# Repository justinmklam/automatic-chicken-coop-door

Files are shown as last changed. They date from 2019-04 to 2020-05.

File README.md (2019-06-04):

# Automatic Chicken Coop Door

Automatic chicken coop door for my backyard egg layers. Modeled after the commercially available [Chicken Guard](https://www.chickenguard.com/).

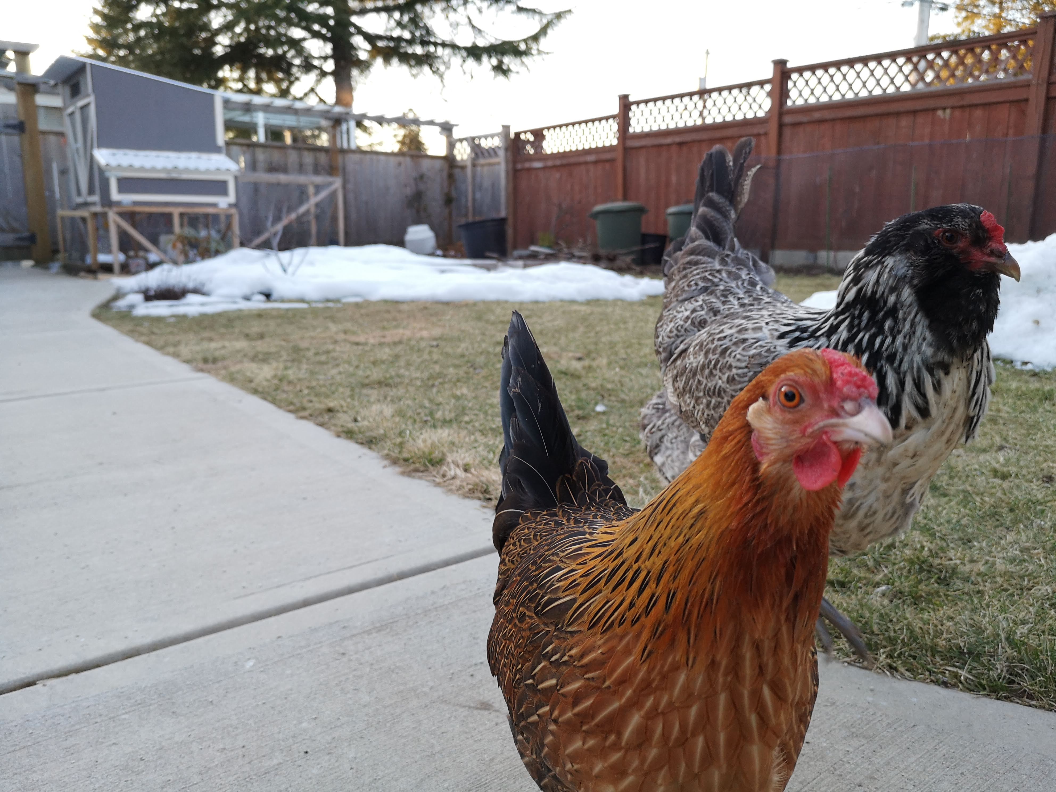
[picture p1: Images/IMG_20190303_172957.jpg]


## Parts List
- Arduino Pro Mini
- Monochrome 128x32 I2C OLED
- DS3231 RTC with CR2032 Battery
- 6V 10rpm 25GA Brushed DC Motor
- TB6612FNG Motor Driver
- XL6009 Buck Boost Module

## Dependencies
- [Low Power](https://github.com/rocketscream/Low-Power)
- [Motor Driver TB6612FNG](https://github.com/sparkfun/SparkFun_TB6612FNG_Arduino_Library)
- [FabioCuomo-DS3231](https://github.com/FabioCuomo/FabioCuomo-DS3231)
- [SSD1306 1.2.9](https://github.com/adafruit/Adafruit_SSD1306)
- [GFX 1.4.2](https://github.com/adafruit/Adafruit-GFX-Library)

## How It Works

The main program sets alarms to wake up from sleep based on sunrise/sunset times (from [here](https://www.timeanddate.com/sun/canada/vancouver?month=1&year=2019)). These times are consistent year after year, and is more reliable than using a light sensor which can be finicky to adjust for street lamps, headlights from passing cars, etc.

## Power Consumption

- Powered on = 18.35 mA
- Motor on = 320 mA (no load), ~700 mA (load)
- Sleep = 0.94 mA

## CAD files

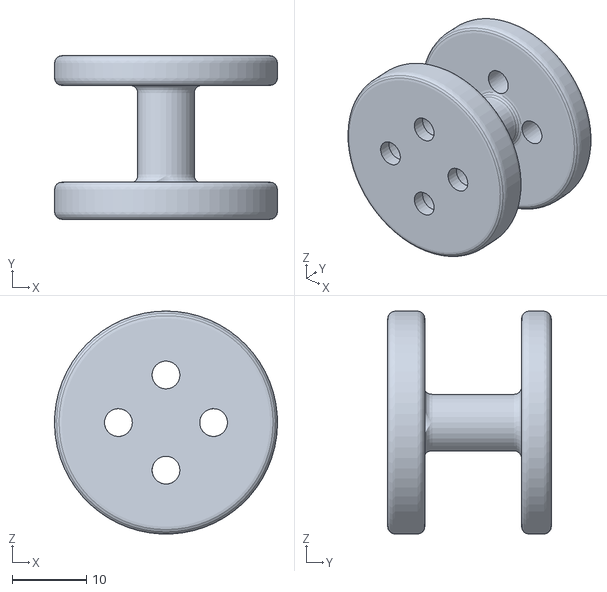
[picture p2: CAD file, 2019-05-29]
CAD/motor-spool.stl
30.0 x 22.0 x 30.0

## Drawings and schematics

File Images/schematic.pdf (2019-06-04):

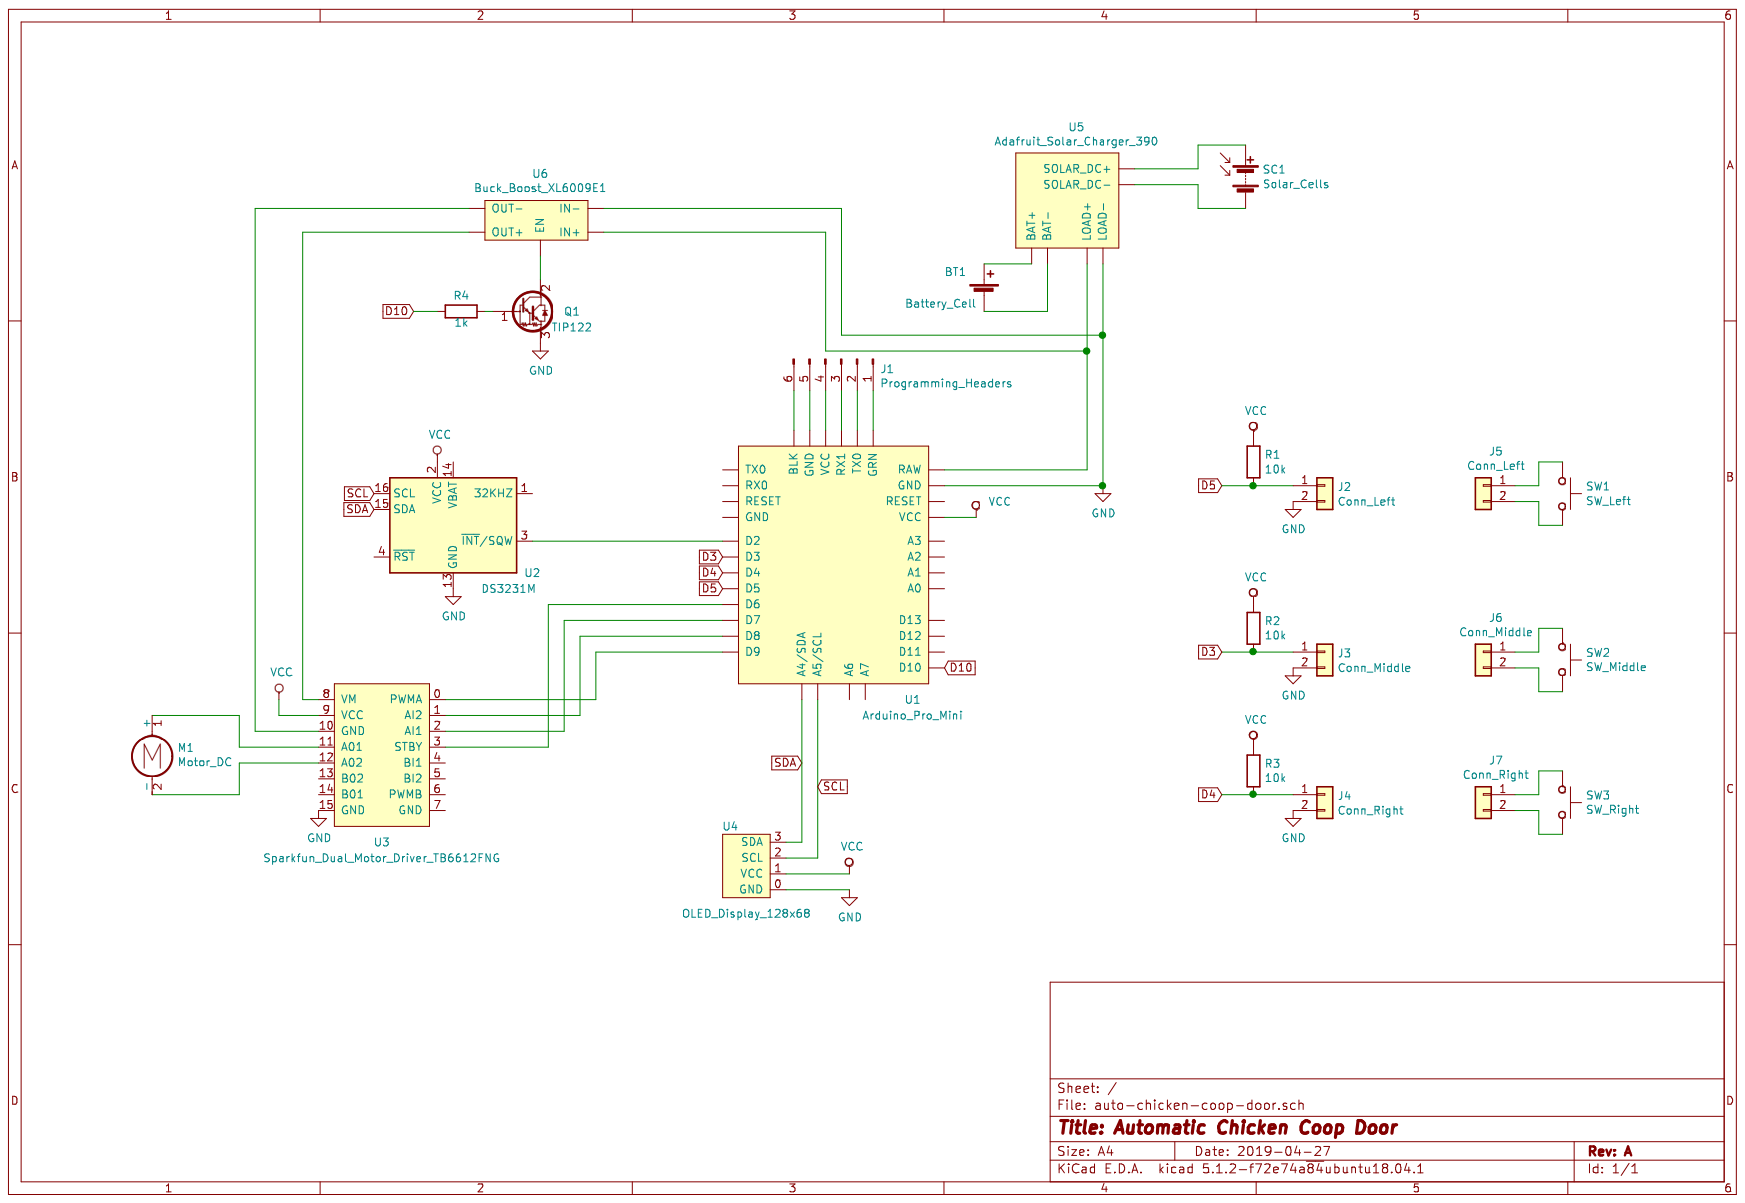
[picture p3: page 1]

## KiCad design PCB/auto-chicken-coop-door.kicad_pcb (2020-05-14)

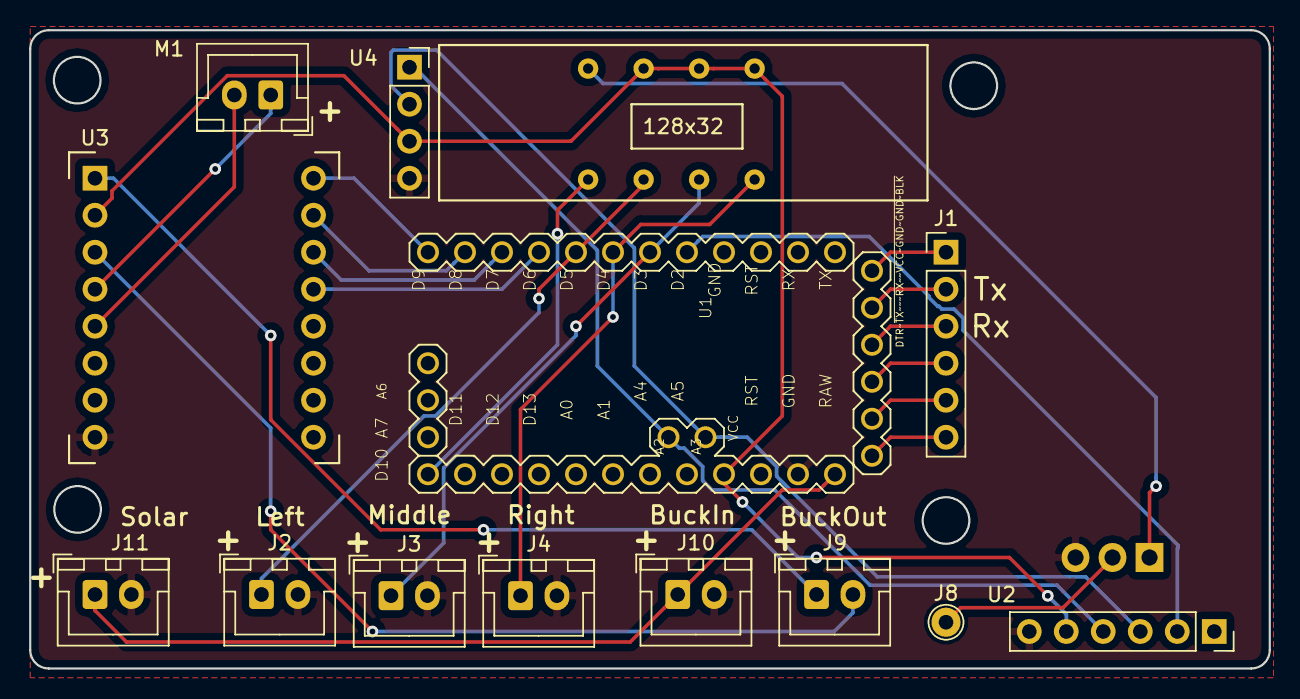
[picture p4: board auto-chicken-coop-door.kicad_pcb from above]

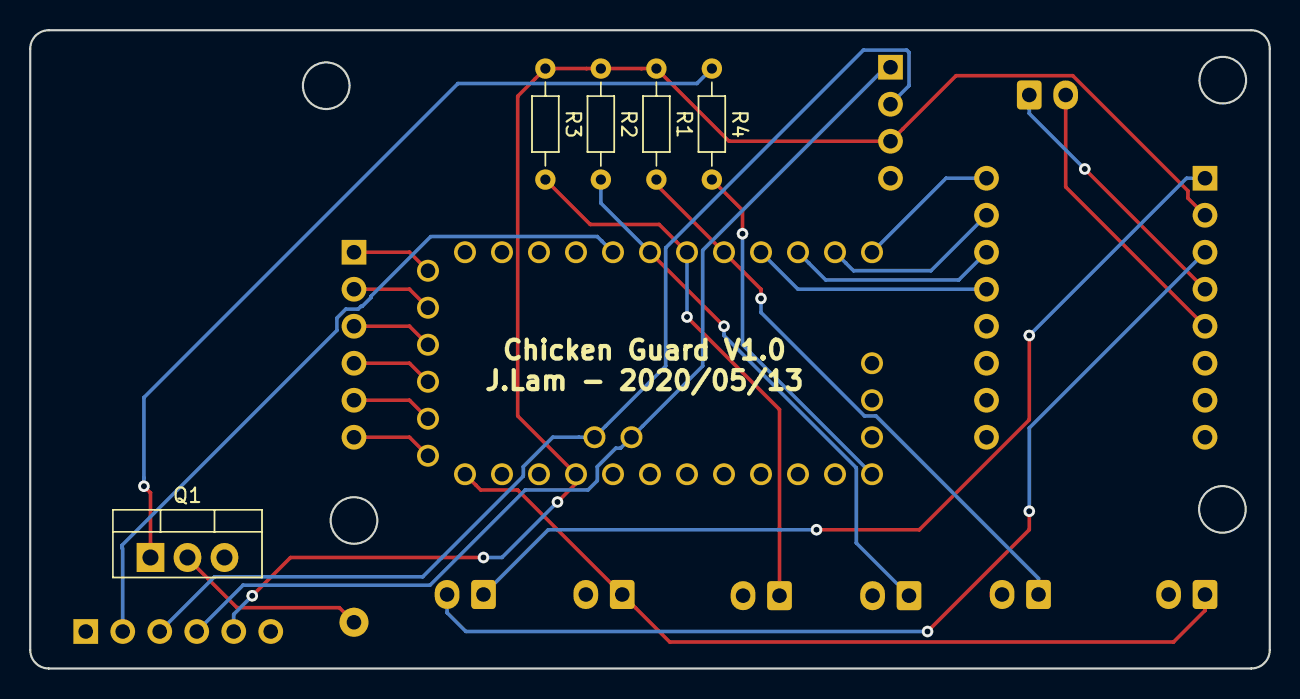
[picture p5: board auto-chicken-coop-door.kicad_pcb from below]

Board: 2 copper layers, 85.1 x 43.8 mm, 18 parts (5 on the bottom side), 26 nets.

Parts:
J1: Programming_Headers; PinHeader_1x06_P2.54mm_Vertical
J2: Conn_Left; JST_XH_B02B-XH-A_1x02_P2.50mm_Vertical
J3: Conn_Middle; JST_XH_B02B-XH-A_1x02_P2.50mm_Vertical
J4: Conn_Right; JST_XH_B02B-XH-A_1x02_P2.50mm_Vertical
J8: Conn_01x01; TestPoint_THTPad_D2.0mm_Drill1.0mm
J9: BuckBoost; JST_XH_B02B-XH-A_1x02_P2.50mm_Vertical
J10, J11: Charger; JST_XH_B02B-XH-A_1x02_P2.50mm_Vertical
M1: Motor_DC; JST_XH_B02B-XH-A_1x02_P2.50mm_Vertical
Q1: TIP122; TO-220-3_Vertical
R1, R2, R3: 10k; R_Axial_DIN0204_L3.6mm_D1.6mm_P7.62mm_Horizontal
R4: 1k; R_Axial_DIN0204_L3.6mm_D1.6mm_P7.62mm_Horizontal
U1: Arduino_Pro_Mini; ArduinoProMini
U2: DS3231; PinSocket_1x06_P2.54mm_Vertical
U3: Sparkfun_Dual_Motor_Driver_TB6612FNG; Sparkfun_TB6612FNG
U4: SSD1306_OLED_128x32; SSD1306_Adafruit_128x32

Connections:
D3: J3.1, R2.2, U1.D3
D4: J4.1, R3.2, U1.D4
D5: J2.1, R1.2, U1.D5
D10: R4.2, U1.D10
GND: J2.2, J3.2, J4.2, J10.2, J11.2, Q1.3, U1.GND@1, U2.6, U3.8, U4.4
unnamed: J1.1, U1.DTR
unnamed: J1.2, U1.TX@1
unnamed: J1.3, U1.RX@1
unnamed: J1.4, U1.VCC@1
unnamed: J1.5, U1.GND@2
unnamed: J1.6, U1.BLK
unnamed: J8.1, Q1.2
unnamed: J9.1, U3.1
unnamed: J9.2, U3.3
unnamed: J10.1, J11.1, U1.RAW
unnamed: M1.1, U3.4
unnamed: M1.2, U3.5
unnamed: Q1.1, R4.1
unnamed: U1.D2, U2.2
unnamed: U1.D6, U3.12
unnamed: U1.D7, U3.11
unnamed: U1.D8, U3.10
unnamed: U1.D9, U3.9
SCL: U1.A5, U2.3, U4.2
SDA: U1.A4, U2.4, U4.1
VCC: R1.1, R2.1, R3.1, U1.VCC, U2.5, U3.2, U4.3

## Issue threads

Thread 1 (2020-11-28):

Power Consumption and door time

sl6der, 2020-11-28:
Hi Justin,
I ordered some of your PCBs and build one of them for my own chicken coop.
I literally found some issues with it.
First of all thank you for sharing your repo.

One of the problems I've gotten is, that the force of my door let spin the motor faster than spinning upwards.
In your code you calculate the average time of up and down spinning.
This code part has to separated, because the open run timing should be longer than downwards (because door weight and force).

Another problem was running into was the power consumption, probably coming from the RTC and overall.
I'm using exactly what you posted in your readme.md, but in sleep the discharge is about 6mAh without RTC and 40-45mAh with RTC.
Do you have any suggestions to this?

The problem with the up and down spinning is a smaller problem, because I can adjust the speed of the forward and backward spinning to come close to the same up and downward time, but the power consumption is a really big mess.

Hopefully you're willing to help me and overwork the code once again?

Thanks for your time and help :)

justinmklam, 2020-12-02:
Thanks for checking out this project! I didn't think anyone would find it, but I actually never ended up finishing this since I eventually had to move and sell my hens. So you're treading in uncharted waters :)

Good catch about the up vs down motor movements. A quick fix could be to add an arbitrary multiplier to the up time, but that might be cumbersome to tune. I unfortunately don't have plans to continue working on this project!

Yes, I removed a few components on the RTC module to reduce the current consumption. I followed [this post](https://sites.google.com/site/wayneholder/low-power-techniques-for-arduino), which I'll copy here for reference:

> Note: to reduce power consumption, I removed the power indication LED on the DS3213 board, the AT24C32D EEPROM, two 4.7K 4x resistor packs that were used as I2C pull up resistors (replaced these with 10K resistors on the breadboard, which you can see just to the left of the AutoPower module) and another resistor that implemented a crude charger circuit for the CR2032 (bad idea!)  The photo below shows modified module where the components that were removed are circled in yellow.  In retrospect, it would have probably been easier just to buy the DS3231 chip, and mount it on an appropriate SMD adapter board, as the IC includes everything you need except for a few bypass caps.  The DS3231M version also comes in an 8 pin form factor, but this version is rated as slightly less accurate than the DS3231.

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

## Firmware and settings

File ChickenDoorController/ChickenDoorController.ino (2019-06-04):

#include <LowPower.h>

#include "EepromExtended.h"
#include "Task.h"
#include "TaskScheduler.h"
#include "SunriseSunsetTimes.h"
#include "Logger.h"

#include "Display_SSD1306.h"
#include "Rtc_DS3231.h"
#include "Motor_TB6612.h"

Rtc rtc;
Ssd1306 display;
MotorTb6612 motor;

const uint8_t ALARM_NUMBER = 1; // two alarms available, but we just need one
const uint8_t ALARM_PIN = 2;    //use interrupt 0 (pin 2) and run function wakeUp when pin 2 gets LOW
const uint8_t LED_PIN = 13;     //use arduino on-board led for indicating sleep or wakeup status

const uint8_t BUTTON_PIN_LEFT = 5;
const uint8_t BUTTON_PIN_MIDDLE = 3;   // must be on hardware interrupt pin
const uint8_t BUTTON_PIN_RIGHT = 4;

const uint8_t MOTOR_TRANSISTOR_PIN = 10;

// Pullup resistor used
const uint8_t BUTTON_STATE_DEFAULT = HIGH;
const uint8_t BUTTON_STATE_PRESSED = LOW;

const uint8_t EEPROM_ADDR_DAYLIGHT_SAVINGS = 0;
const uint8_t EEPROM_ADDR_DOOR_STATUS = 1;
const uint8_t EEPROM_ADDR_DOOR_DISTANCE = 2; // This takes 4 registers since 32 bit value

bool DOOR_STATE_OPEN = EEPROMRead8bit(EEPROM_ADDR_DOOR_STATUS);
uint32_t DOOR_OPEN_CLOSE_DISTANCE = EEPROMRead32bit(EEPROM_ADDR_DOOR_DISTANCE);
bool DAYLIGHT_SAVING_TIME_ENABLED = EEPROMRead8bit(EEPROM_ADDR_DAYLIGHT_SAVINGS);

const uint16_t REFRESH_INTERVAL_MS = 100;

int NEXT_ALARM_HOUR = 0;
int NEXT_ALARM_MINUTE = 0;

/*************************************************************************/

class UpdateDisplay : public TimedTask
{
public:
  UpdateDisplay();
  virtual void run(uint32_t now);
  void pauseMainScreen();
  void resumeMainScreen();

private:
  bool pauseUpdate = false;
  const uint16_t intervalDisplayRefresh = 1000;

  // TODO: This buffer is currently causing weird artifacts to show. Reducing to 5
  // causes it to crash (but artifacts are gone), but >6 is functional. Weird.
  char bufferTimestamp[10];
};

UpdateDisplay::UpdateDisplay() : TimedTask(millis())
{
  display.begin();
}

void UpdateDisplay::pauseMainScreen()
{
  loggerln("UpdateDisplay.pauseMainScreen");
  pauseUpdate = true;
}

void UpdateDisplay::resumeMainScreen()
{
  loggerln("UpdateDisplay.resumeMainScreen");
  pauseUpdate = false;
}

void UpdateDisplay::run(uint32_t now)
{
  if (!pauseUpdate)
  {
    display.clear();
    rtc.get_timestamp_str(bufferTimestamp);
    display.println(bufferTimestamp);
    display.print(NEXT_ALARM_HOUR);
    display.print(":");
    display.print(NEXT_ALARM_MINUTE);
    display.print(" ALRM");
    display.show();
  }

  incRunTime(intervalDisplayRefresh);
}

/*************************************************************************/

class DoorControl : public TriggeredTask
{
public:
  DoorControl();
  void open();
  void close();
  void setOpen();
  void setClose();
  virtual void run(uint32_t now);

private:
  void enableMotorPower();
  void disableMotorPower();
  bool setDoorOpen = false;
  bool setDoorClose = false;
};

DoorControl::DoorControl() : TriggeredTask()
{
  disableMotorPower();
}

void DoorControl::run(uint32_t now)
{
  if (setDoorOpen)
  {
    open();
    setDoorOpen = false;
  }
  else if (setDoorClose)
  {
    close();
    setDoorClose = false;
  }

  resetRunnable();
}

void DoorControl::enableMotorPower()
{
  digitalWrite(MOTOR_TRANSISTOR_PIN, LOW);
}

void DoorControl::disableMotorPower()
{
  digitalWrite(MOTOR_TRANSISTOR_PIN, HIGH);
}

void DoorControl::setOpen()
{
  loggerln("DoorControl.setOpen");
  setDoorOpen = true;
}

void DoorControl::setClose()
{
  loggerln("DoorControl.setClose");
  setDoorClose = true;
}

void DoorControl::open()
{
  if (DOOR_STATE_OPEN)
  {
    loggerln("DoorControl: Already open");
    return;
  }

  for (int i = 0; i < DOOR_OPEN_CLOSE_DISTANCE; i++)
  {
    enableMotorPower();
    motor.up();
    delay(REFRESH_INTERVAL_MS);
  }

  motor.brake();
  disableMotorPower();
  DOOR_STATE_OPEN = true;
  EEPROMWrite8bit(EEPROM_ADDR_DOOR_STATUS, DOOR_STATE_OPEN);
  loggerln("DoorControl: Opened");
}

void DoorControl::close()
{
  if (!DOOR_STATE_OPEN)
  {
    loggerln("DoorControl: Already closed");
    return;
  }

  for (int i = 0; i < DOOR_OPEN_CLOSE_DISTANCE; i++)
  {
    enableMotorPower();
    motor.down();
    delay(REFRESH_INTERVAL_MS);
  }

  motor.brake();
  disableMotorPower();
  DOOR_STATE_OPEN = false;
  EEPROMWrite8bit(EEPROM_ADDR_DOOR_STATUS, DOOR_STATE_OPEN);
  loggerln("DoorControl: Closed");
}

/*************************************************************************/

class SleepMode : public TriggeredTask
{
public:
  SleepMode(DoorControl *_ptrDoorControl);
  void enableSleepFromAlarm(uint8_t hour, uint8_t minute);
  void enableSleepFromUserInactivity();
  virtual void run(uint32_t now);

private:
  bool isAlarmTriggered = false;
  bool enableSleep = false;
  bool sleepFromAlarm = false;
  bool sleepFromUserInactivity = false;

  uint8_t alarmHour, alarmMinute;

  bool controlDoorFromAlarm();
  void attachPinInterrupt(uint8_t pinNumber);
  void detachPinInterrupt(uint8_t pinNumber);
  void powerDown();
  void wakeUp();
  static void wakeUpInterruptHandler();

  DoorControl *ptrDoorControl;
};

SleepMode::SleepMode(DoorControl *_ptrDoorControl) : TriggeredTask(),
                                                     ptrDoorControl(_ptrDoorControl)

{
  //Set pin D2 as INPUT for accepting the interrupt signal from DS3231
  pinMode(ALARM_PIN, INPUT);
  rtc.begin();
}

void SleepMode::run(uint32_t now)
{
  // NO LOG STATEMENTS ALLOWED HERE

  if (sleepFromAlarm)
  {
    attachPinInterrupt(ALARM_PIN);

    enableSleep = true;
  }
  if (sleepFromUserInactivity)
  {
    attachPinInterrupt(BUTTON_PIN_MIDDLE);

    enableSleep = true;
  }

  if (enableSleep)
  {
    powerDown();
    wakeUp(); // Resumes here after sleep

    if (sleepFromAlarm)
    {
      isAlarmTriggered = controlDoorFromAlarm();

      if (isAlarmTriggered)
      {
        rtc.clear_alarm(ALARM_NUMBER);
        detachPinInterrupt(ALARM_PIN);

        sleepFromAlarm = false;
      }
    }
    if (sleepFromUserInactivity)
    {
      detachPinInterrupt(BUTTON_PIN_MIDDLE);
      sleepFromUserInactivity = false;
    }
  }

  resetRunnable();
}

void SleepMode::enableSleepFromAlarm(uint8_t hour, uint8_t minute)
{
  logger("SleepMode.enableSleepFromAlarm: ");
  logger(hour);
  logger(":");
  loggerln(minute);

  alarmHour = hour;
  alarmMinute = minute;
  NEXT_ALARM_HOUR = hour;
  NEXT_ALARM_MINUTE = minute;
  sleepFromAlarm = true;

  rtc.set_alarm(ALARM_NUMBER, hour, minute, 0);
}

bool SleepMode::controlDoorFromAlarm()
{
  // NO LOG STATEMENTS ALLOWED HERE

  bool alarmTriggered = false;

  // Check if woken up by alarm
  if (rtc.now().hour() == alarmHour && rtc.now().minute() == alarmMinute)
  {
    alarmTriggered = true;
    // Before noon is morning, so open door
    if (rtc.now().hour() < 12)
    {
      ptrDoorControl->setOpen();
      ptrDoorControl->setRunnable();
    }
    else
    {
      ptrDoorControl->setClose();
      ptrDoorControl->setRunnable();
    }
  }
  return alarmTriggered;
}

void SleepMode::enableSleepFromUserInactivity()
{
  loggerln("SleepMode.enableSleepFromUserInactivity");

  sleepFromUserInactivity = true;
}

void SleepMode::attachPinInterrupt(uint8_t pinNumber)
{
  logger("SleepMode.attachPinInterrupt: ");
  loggerln(pinNumber);

  attachInterrupt(
      digitalPinToInterrupt(pinNumber),
      wakeUpInterruptHandler,
      CHANGE);
}

void SleepMode::detachPinInterrupt(uint8_t pinNumber)
{
  logger("SleepMode.detachPinInterrupt: ");
  loggerln(pinNumber);

  detachInterrupt(digitalPinToInterrupt(pinNumber));
}

void SleepMode::powerDown()
{
  loggerln("SleepMode.powerDown");

  display.sleep();
  LowPower.powerDown(SLEEP_FOREVER, ADC_OFF, BOD_OFF);
}

void SleepMode::wakeUp()
{
  display.wake();
}

void SleepMode::wakeUpInterruptHandler() // here the interrupt is handled after wakeup
{
}

/*************************************************************************/

class SunriseSunsetAlarms : public TimedTask
{
public:
  SunriseSunsetAlarms(SleepMode *_ptrSleep);
  void setAlarm();
  virtual void run(uint32_t now);

private:
  const uint32_t alarmUpdateIntervalMs = 5000;
  const uint8_t sunriseBufferHour = 0;
  const uint8_t sunsetBufferHour = 1;
  SleepMode *ptrSleep;
};

SunriseSunsetAlarms::SunriseSunsetAlarms(SleepMode *_ptrSleep)
    : TimedTask(millis()),
      ptrSleep(_ptrSleep)
{
}

void SunriseSunsetAlarms::run(uint32_t now)
{
  setAlarm();
  incRunTime(alarmUpdateIntervalMs);
}

void SunriseSunsetAlarms::setAlarm()
{
  // loggerln("SunriseSunsetAlarms.setAlarm");

  // TODO: Handle daylight savings time (since sunrise/sunset times do)
  uint8_t currentMonthIndex = rtc.now().month() - 1;
  uint8_t currentHour = rtc.now().hour();
  uint8_t currentMinute = rtc.now().minute();
  uint8_t alarmHour, alarmMinute;

  bool isBeforeSunrise = (currentHour < SUNRISE_TIMES[currentMonthIndex].hour) ||
                         ((currentHour == SUNRISE_TIMES[currentMonthIndex].hour) &&
                          (currentMinute < SUNRISE_TIMES[currentMonthIndex].minute));

  bool isAfterSunset = (currentHour > SUNSET_TIMES[currentMonthIndex].hour) ||
                       ((currentHour == SUNSET_TIMES[currentMonthIndex].hour) &&
                        (currentMinute >= SUNSET_TIMES[currentMonthIndex].minute));

  if (isBeforeSunrise || isAfterSunset)
  {
    alarmHour = SUNRISE_TIMES[currentMonthIndex].hour - sunriseBufferHour;
    alarmMinute = SUNRISE_TIMES[currentMonthIndex].minute;
  }
  else
  {
    alarmHour = SUNSET_TIMES[currentMonthIndex].hour + sunsetBufferHour;
    alarmMinute = SUNSET_TIMES[currentMonthIndex].minute;
  }

  ptrSleep->enableSleepFromAlarm(alarmHour, alarmMinute);
}

/*************************************************************************/

class UserInput : public TimedTask
{
public:
  UserInput(SleepMode *_ptrSleep, UpdateDisplay *_ptrDisplay, DoorControl *_ptrDoorControl);
  virtual void run(uint32_t now);

private:
  void checkInactivity(bool isButtonPressed);
  void calibrateDoor();
  void setDaylightSavingTime();

  uint8_t userState = 0;

  bool calibrationMode = false;
  bool isButtonPressed = false;

  uint8_t buttonStateLeft = BUTTON_STATE_DEFAULT;
  uint8_t buttonStateMid = BUTTON_STATE_DEFAULT;
  uint8_t buttonStateRight = BUTTON_STATE_DEFAULT;

  uint32_t previousMillis;
  uint32_t inactivityCounter = 0;
  uint32_t calibrationButtonPressedCounter = 0;
  uint32_t doorCalibrationDistance = 0;

  const uint16_t calibrationButtonPressedThreshold = 20;
  const uint16_t daylightSavingsButtonPressedThreshold = 30;
  const uint16_t intervalInactive = 100;

  SleepMode *ptrSleep;
  UpdateDisplay *ptrDisplay;
  DoorControl *ptrDoorControl;
};

UserInput::UserInput(SleepMode *_ptrSleep, UpdateDisplay *_ptrDisplay, DoorControl *_ptrDoorControl) : TimedTask(millis()),
                                                                                                       ptrSleep(_ptrSleep),
                                                                                                       ptrDisplay(_ptrDisplay),
                                                                                                       ptrDoorControl(_ptrDoorControl)
{
  pinMode(BUTTON_PIN_LEFT, INPUT);
  pinMode(BUTTON_PIN_MIDDLE, INPUT);
  pinMode(BUTTON_PIN_RIGHT, INPUT);

  previousMillis = millis();
}

void UserInput::run(uint32_t now)
{
  buttonStateLeft = digitalRead(BUTTON_PIN_LEFT);
  buttonStateMid = digitalRead(BUTTON_PIN_MIDDLE);
  buttonStateRight = digitalRead(BUTTON_PIN_RIGHT);

  isButtonPressed = buttonStateLeft == BUTTON_STATE_PRESSED || buttonStateMid == BUTTON_STATE_PRESSED || buttonStateRight == BUTTON_STATE_PRESSED;

  if (calibrationMode == true)
  {
    calibrateDoor();
  }
  else
  {
    if (buttonStateMid == BUTTON_STATE_PRESSED)
    {
      calibrationButtonPressedCounter++;

      // Super long press is to enable/disable daylight savings
      if (calibrationButtonPressedCounter >= daylightSavingsButtonPressedThreshold)
      {
        display.clear();
        display.println("Toggle DST");
        display.show();
      }
      // Regular long press is to enter calibration mode
      else if (calibrationButtonPressedCounter >= calibrationButtonPressedThreshold)
      {
        ptrDisplay->pauseMainScreen();

        display.clear();
        display.println("Calibrate");
        display.show();
      }
    }
    else
    {
      // Enter the different modes on button release
      if (calibrationButtonPressedCounter >= daylightSavingsButtonPressedThreshold)
      {
        calibrationButtonPressedCounter = 0;

        delay(1000);

        setDaylightSavingTime();
      }
      else if (calibrationButtonPressedCounter >= calibrationButtonPressedThreshold)
      {
        calibrationButtonPressedCounter = 0;
        calibrationMode = true;

        delay(1000);
      }
    }

    if (buttonStateLeft == BUTTON_STATE_PRESSED)
    {
      ptrDoorControl->setOpen();
      ptrDoorControl->setRunnable();
    }
    else if (buttonStateRight == BUTTON_STATE_PRESSED)
    {
      ptrDoorControl->setClose();
      ptrDoorControl->setRunnable();
    }
  }

  checkInactivity(isButtonPressed);
  incRunTime(REFRESH_INTERVAL_MS);
}

void UserInput::setDaylightSavingTime()
{
  display.clear();

  if (DAYLIGHT_SAVING_TIME_ENABLED)
  {
    display.println("DST > OFF");
    rtc.set_daylight_saving_time(false);
    DAYLIGHT_SAVING_TIME_ENABLED = false;
    EEPROMWrite8bit(EEPROM_ADDR_DAYLIGHT_SAVINGS, false);
  }
  else
  {
    display.println("DST > ON");
    rtc.set_daylight_saving_time(true);
    DAYLIGHT_SAVING_TIME_ENABLED = true;
    EEPROMWrite8bit(EEPROM_ADDR_DAYLIGHT_SAVINGS, true);
  }

  display.show();

  delay(2000);

  ptrDisplay->resumeMainScreen();
}

void UserInput::calibrateDoor()
{
  switch (userState)
  {
  default:
    display.clear();
    display.println("Move up");
    display.print("Next >");
    display.show();

    delay(250);

    userState++;

    break;

  case 1:
    buttonStateLeft = digitalRead(BUTTON_PIN_LEFT);
    buttonStateMid = digitalRead(BUTTON_PIN_MIDDLE);
    buttonStateRight = digitalRead(BUTTON_PIN_RIGHT);

    if (buttonStateLeft == BUTTON_STATE_PRESSED)
    {
      motor.down();
    }
    else if (buttonStateRight == BUTTON_STATE_PRESSED)
    {
      motor.up();
    }
    else
    {
      motor.brake();
    }

    if (buttonStateMid == BUTTON_STATE_PRESSED)
    {
      doorCalibrationDistance = 0;

      display.clear();
      display.println("Move down");
      display.print("Next >");
      display.show();

      delay(250);

      userState++;
    }

    break;

  case 2:
    buttonStateLeft = digitalRead(BUTTON_PIN_LEFT);
    buttonStateMid = digitalRead(BUTTON_PIN_MIDDLE);
    buttonStateRight = digitalRead(BUTTON_PIN_RIGHT);

    if (buttonStateLeft == BUTTON_STATE_PRESSED)
    {
      motor.down();
      doorCalibrationDistance++;
    }
    else if (buttonStateRight == BUTTON_STATE_PRESSED)
    {
      if (doorCalibrationDistance > 0)
      {
        motor.up();
        doorCalibrationDistance--;
      }
      else
      {
        motor.brake();
      }
    }
    else
    {
      motor.brake();
    }

    if (buttonStateMid == BUTTON_STATE_PRESSED)
    {
      display.clear();

      if (doorCalibrationDistance != 0)
      {
        DOOR_OPEN_CLOSE_DISTANCE = doorCalibrationDistance;

        display.println("Complete");
        display.print(DOOR_OPEN_CLOSE_DISTANCE);
        display.show();

        EEPROMWrite32bit(EEPROM_ADDR_DOOR_DISTANCE, DOOR_OPEN_CLOSE_DISTANCE);
        DOOR_STATE_OPEN = false;
      }
      else
      {
        display.println("Calibrate\nskipped");
        display.show();
      }

      delay(1000);

      userState++;
    }

    break;

  case 3:
    userState = 0;
    calibrationMode = false;
    ptrDisplay->resumeMainScreen();

    break;
  }
}

void UserInput::checkInactivity(bool isButtonPressed)
{
  // Don't sleep during calibration mode
  if (calibrationMode) {
    return;
  }
  else if (isButtonPressed)
  {
    inactivityCounter = 0;
  }
  else
  {
    inactivityCounter++;

    if (inactivityCounter >= intervalInactive)
    {
      loggerln("UserInput.checkInactivity: Detected");

      inactivityCounter = 0;

      ptrSleep->enableSleepFromUserInactivity();
      ptrSleep->setRunnable();
    }
  }
}

/*************************************************************************/

void setup()
{
  loggerBegin();
}

void loop()
{

  loggerln("main: Starting");

  UpdateDisplay updateDisplay;
  DoorControl doorControl;
  SleepMode sleepMode(&doorControl);
  SunriseSunsetAlarms sunAlarms(&sleepMode);
  UserInput userInput(&sleepMode, &updateDisplay, &doorControl);

  // Order determines task priority
  Task *tasks[] = {
      &userInput,
      &updateDisplay,
      &sleepMode,
      &doorControl,
      &sunAlarms};

  TaskScheduler scheduler(tasks, NUM_TASKS(tasks));

  loggerln("main: Running tasks");
  scheduler.runTasks();
}

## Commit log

2019-03-03 Add test code for controlling motor driver
2019-03-04 Add motor firmware settings from config utility
    [jrk21v3_motor_config.txt]
2019-03-09 Refactor motor control methods and base sketch
2019-03-09 Refactor motor control to class
2019-03-15 Add 3D print models for motor spool
    [motor-spool.stl]
2019-03-20 Add arduino libraries to path
2019-03-20 Use RTClibExtended for alarms; add low power example
2019-03-22 Add wrapper class for motor control
    Should refactor class to use inheritance instead
2019-03-23 Add basic button functionality
2019-03-23 Add proper display sleep method
    Reduces sleep consumption from ~2mA to ~0.8mA
2019-03-23 Fix millis() interval check to handle rollover
2019-03-25 Add preliminary door calibration method
2019-04-09 Implement basic door open/close and calibration method
2019-04-09 Save calibrated distance to eeprom
2019-04-09 Activate calibration after 2 second button press
2019-04-09 Move door calibration to separate function
2019-04-09 Rename constants to upper case
2019-04-10 [bugfix] Correct current time check so next alarm is set correctly
2019-04-10 Rename driver files
2019-04-10 Move jrk21v3 config to sketch folder
    [jrk21v3_motor_config.txt]
2019-04-10 Move jrk21v3 demo to separate repository
    [jrk21v3_motor_config.txt]
2019-04-10 [bugfix] Add logic check for before sunrise/after sunset
    Previously would fail if since both minute and hour had to be greater
    (which is incorrect)
    [ChickenDoorController.ino]
2019-04-11 [bugfix] Subtle fix so before sunrise check is correct
    [ChickenDoorController.ino]
2019-04-11 [major] Add daylight saving button toggle
    Also had to disable the logger since it was causing the scheduler to
    fail halfway (for some unknown reason)
    [ChickenDoorController.ino]
2019-04-14 Don't write door calibration if unchanged
2019-04-14 Fix motor direction to consistent behaviour
    [ChickenDoorController.ino]
2019-04-14 Add delay after each calibration state change
    Also don't trigger inactivity monitor during calibration mode
2019-04-14 Reverse motor direction so it's correct with open/close of door
2019-04-28 Initial commit for KiCad schematic files
    [auto-chicken-coop-door.kicad_pcb, auto-chicken-coop-door.sch]
2019-04-28 Change buttons to connectors
    [auto-chicken-coop-door.sch]
2019-04-28 Add pushbuttons; add motor input voltage to 7.5V
    [auto-chicken-coop-door.sch]
2019-04-28 Update title block info
    [auto-chicken-coop-door.sch]
2019-04-28 Add schematic pdf
2019-05-29 Update motor spool model for 3D printing
    [motor-spool.stl]
2019-05-29 Add TIP122 and buck/boost module to schematic
    [auto-chicken-coop-door.sch]
2019-05-29 Add motor power transistor
2019-05-29 Update schematic
2019-05-29 Resave kicad files from crash
    [auto-chicken-coop-door.sch]
2019-05-29 [bugfix] Middle button must be on pin 3 for interrupt
    [ChickenDoorController.ino]
2019-05-29 Remove logger statements causing issues
    Reduce the number of serial prints at the beginning, otherwise it crashes
    [ChickenDoorController.ino]
2019-05-29 Update pin definitions
2019-06-04 Disable motor in constructor; reverse logic
    Use NPN transistor to enable/disable the XL6009 buck/boost converter
    [ChickenDoorController.ino]
2019-06-04 Add parts and power consumption to README
2019-06-04 Update schematic with pins and correct transistor config
    Use TIP122 to enable/disable the XL6009 module. Doesn't work if enable is connected
    directly to pin 10.
    [auto-chicken-coop-door.sch]
2020-05-14 Add footprints to schematic
    [auto-chicken-coop-door.kicad_pcb, auto-chicken-coop-door.sch]
2020-05-14 PCB layout complete
    [auto-chicken-coop-door.kicad_pcb, auto-chicken-coop-door.sch]
2020-05-14 Add silkscreen labels
    [auto-chicken-coop-door.kicad_pcb]
2020-05-14 Add gerbers
    [auto-chicken-coop-door-B.Cu.gbr, auto-chicken-coop-door-B.Mask.gbr, auto-chicken-coop-door-B.Paste.gbr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]
2020-05-14 Add ground plane
    [auto-chicken-coop-door.kicad_pcb]
2020-05-14 Export gerbers
    [auto-chicken-coop-door-B.Cu.gbr, auto-chicken-coop-door-B.Mask.gbr, auto-chicken-coop-door-B.Paste.gbr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]
2020-05-14 Fix overlapping traces with pad
    [auto-chicken-coop-door-B.Cu.gbr, auto-chicken-coop-door-B.Mask.gbr, auto-chicken-coop-door-B.Paste.gbr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]
